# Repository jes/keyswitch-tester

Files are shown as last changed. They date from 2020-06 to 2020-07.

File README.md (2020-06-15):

# Automatic keyboard switch tester

This is the code and CAD for the automatic keyboard switch tester.

You can learn more in my blog post at https://incoherency.co.uk/blog/stories/keyswitch-tester.html

It is not spectacularly well designed, so if you want to make one you might instead consider designing an improved version.

You can [watch a video of it in action](https://www.youtube.com/watch?v=jl0PIKjTmjM).

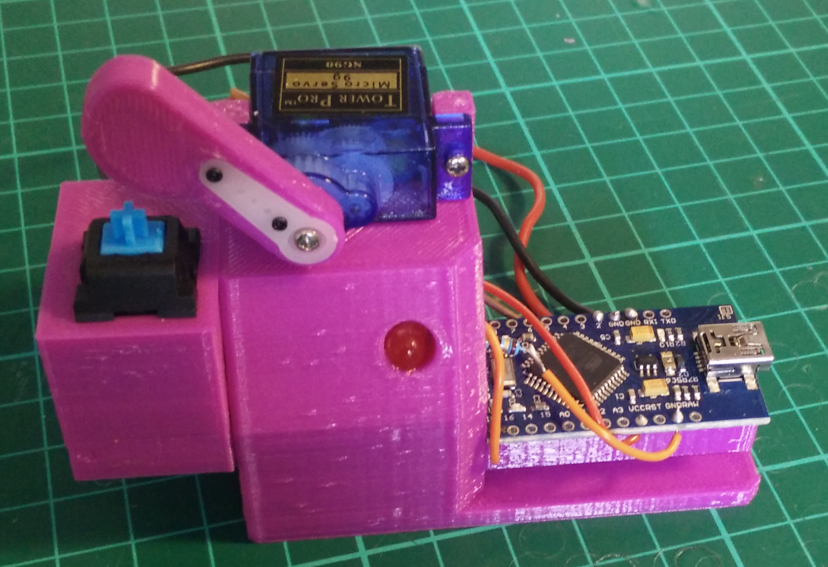
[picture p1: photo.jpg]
Photograph of device


## Assembly instructions

Print 1 each of servohorn.stl, keyswitch-tester.stl, and a holder for whatever type of switch you're using (e.g. cherry-holder.stl).

If you need to make a custom switch holder, you can either start from scratch, or start from BlankHolder in keyswitch-tester.FCStd, or
start from blank-holder.stl in other CAD software. Remember that in addition to holding the switch, you also need to be able to
route wires out.

You'll also need:

 - 1x micro servo (Tower Pro SG90 or compatible)
 - 1x Arduino (I suggest Nano, Pro Micro, or similar)
 - Some short lengths of wire

Optional:

 - 5x M3 threaded insert
 - 1x LED
 - 1x resistor for the LED (e.g. 470 Ohm)

Fit the threaded inserts to the main body by holding them with tweezers while pressing down gently with a hot soldering iron. If you don't
want to use threaded inserts you can just use slightly larger screws and thread directly into the plastic. The hole is about 4mm across.

Super-glue the Arduino to the lower deck, and the LED into the hole. Screw the servo to the mounts on the upper deck. Screw the servo
arm extension on to the servo horn, and fit it to the servo.

Solder the black/brown wire from the servo to one of the GND pins, the red wire to the VCC pin, and the yellow/orange wire
to pin 9.

Solder the resistor to the negative lead of the LED, and a wire from the resistor to another GND pin. Solder the positive lead
of the LED to pin 10. If you don't want to use an LED, the device will still work, you just won't get visual feedback of when
the switch has been pressed.

Solder a loose wire to another GND pin, and another loose wire to pin 2. Solder the other end of the loose wires to whatever
switch you're trying to test. Remain mindful of the fact that you need to be able to fit the switch in the holder, so do these
operations in a sensible order.

Fit your switch to your holder, and screw it to the end plate of the tester.

## Usage instructions

Plug in the Arduino and upload the code. If the servo is stalling, or is not moving through the correct range of motion, then you can
either remove and re-fit the servo arm at a different angle, or adjust the "servomin" and "servomax" parameters in the code.

Once it's clicking your switch properly (which you can verify by looking at the LED you fitted), then you can connect your logging
program to the USB serial port to collect data.

## Contributing

Please contribute any and all changes or fixes. If your contribution does not conveniently fit with the rest of the project, I'll stick
it in a `contrib/` directory so that other people can still get it.

I'm particularly interested in holders for different types of switch, and an improved design for the main body of the tester that meets either
or both of the following:

1. use less plastic (print faster)

2. allow the servo arm to reach its full range of motion instead of crashing into the deck

## Contact

You can email me at james@incoherency.co.uk, or read my blog at https://incoherency.co.uk/

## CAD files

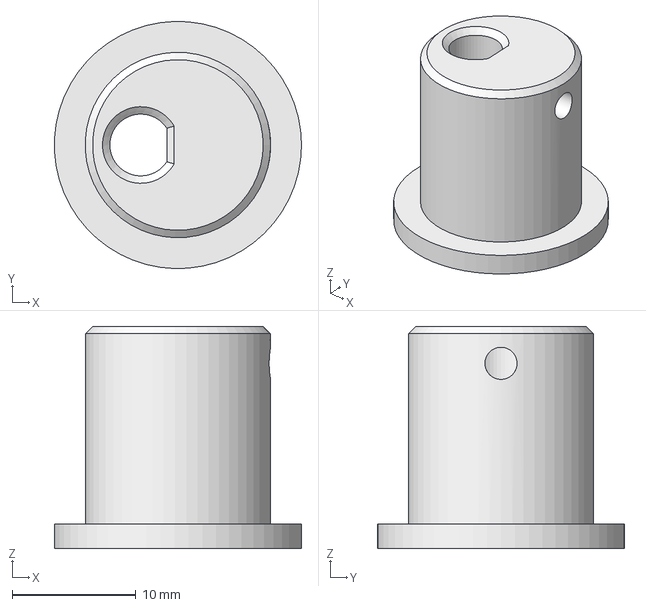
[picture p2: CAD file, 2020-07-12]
bigmachine/eccentricbush.FCStd
20.0 x 20.0 x 18.0 mm

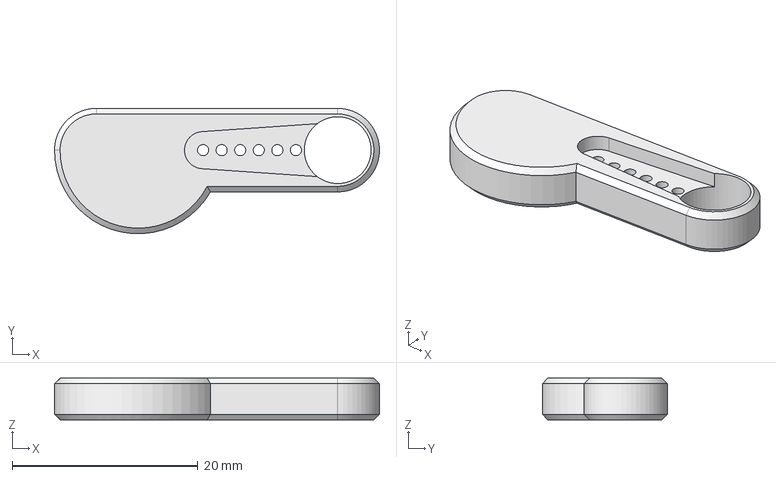
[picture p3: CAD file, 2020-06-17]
servohorn.FCStd
35.0 x 13.5 x 4.50 mm

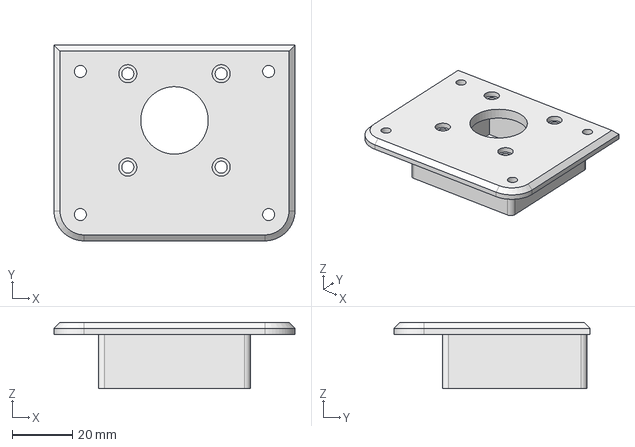
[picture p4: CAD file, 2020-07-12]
bigmachine/steppermount.FCStd
80.0 x 65.0 x 22.0 mm

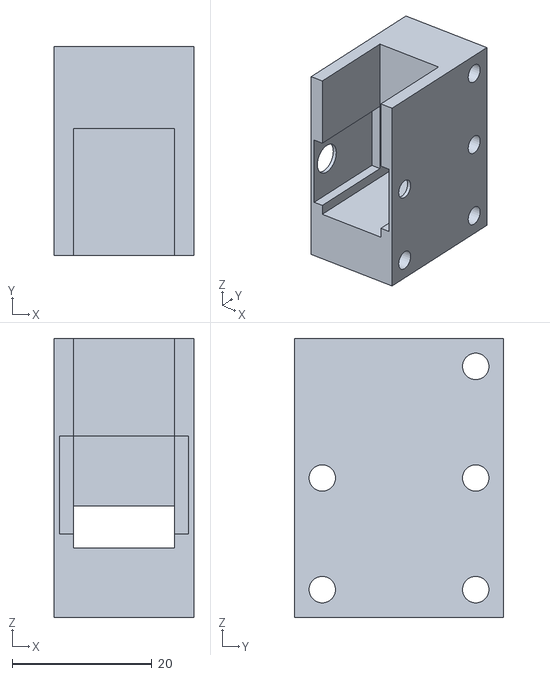
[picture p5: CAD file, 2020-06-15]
jes-holder.stl
20.0 x 30.0 x 40.0

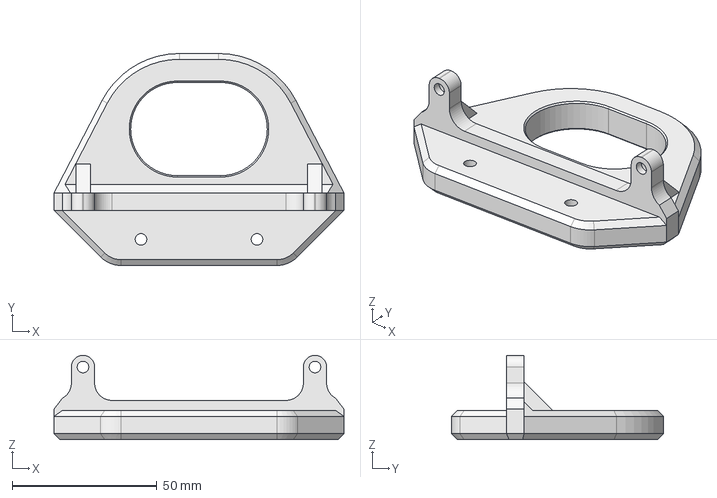
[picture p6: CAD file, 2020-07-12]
bigmachine/yoke.FCStd
100.0 x 73.1 x 29.0 mm

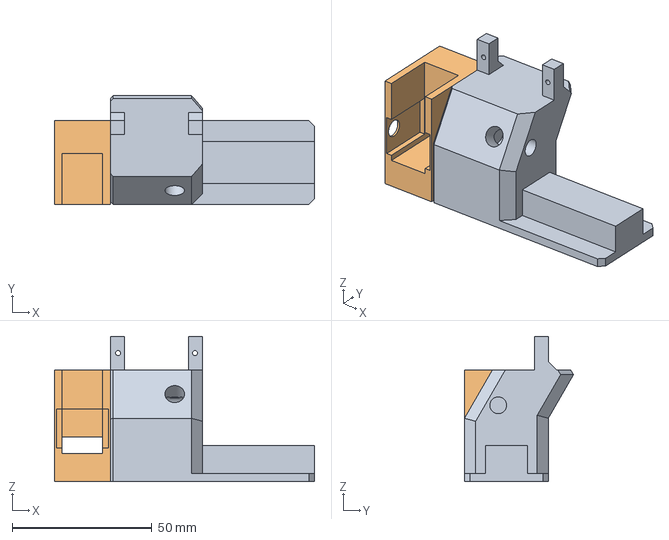
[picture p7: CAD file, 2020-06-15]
keyswitch-tester.FCStd
93.0 x 39.0 x 52.0 mm
JesHolder

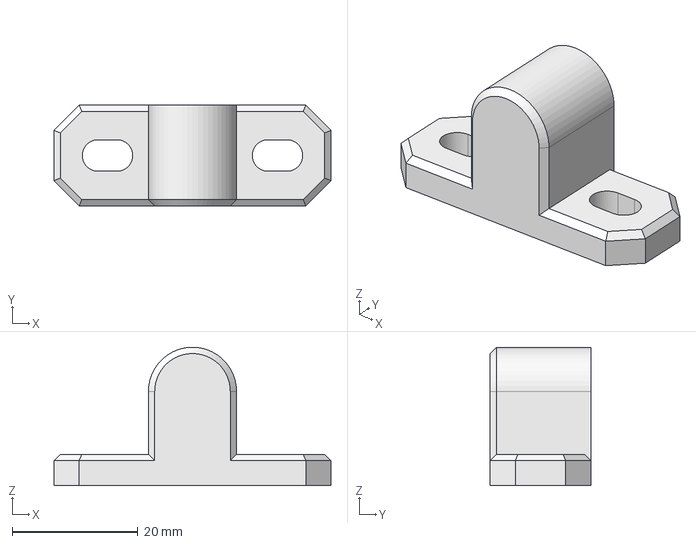
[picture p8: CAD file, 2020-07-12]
bigmachine/rodmount.FCStd
44.0 x 16.0 x 22.0 mm

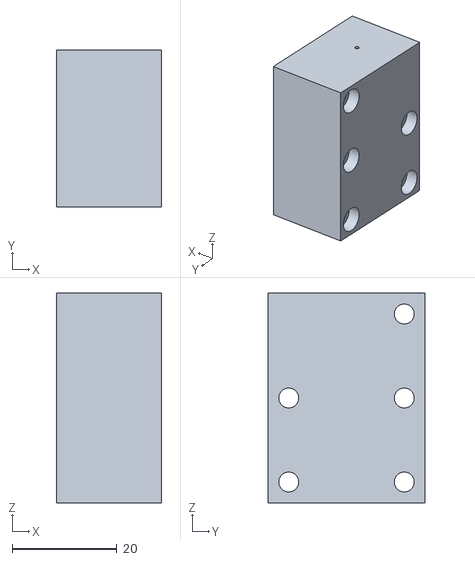
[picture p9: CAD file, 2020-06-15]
blank-holder.stl
20.0 x 30.0 x 40.0

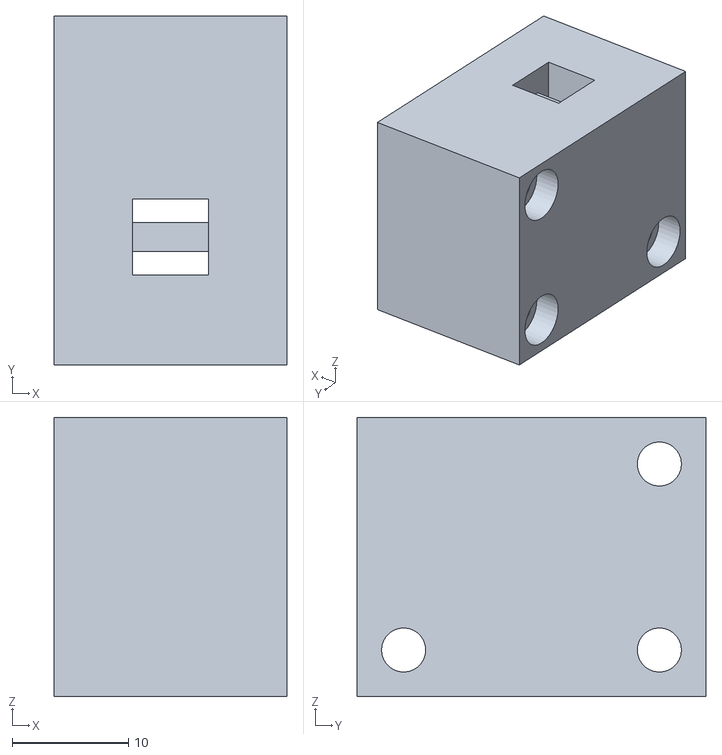
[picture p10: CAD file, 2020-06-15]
6mm-microswitch-holder.stl
20.0 x 30.0 x 24.0

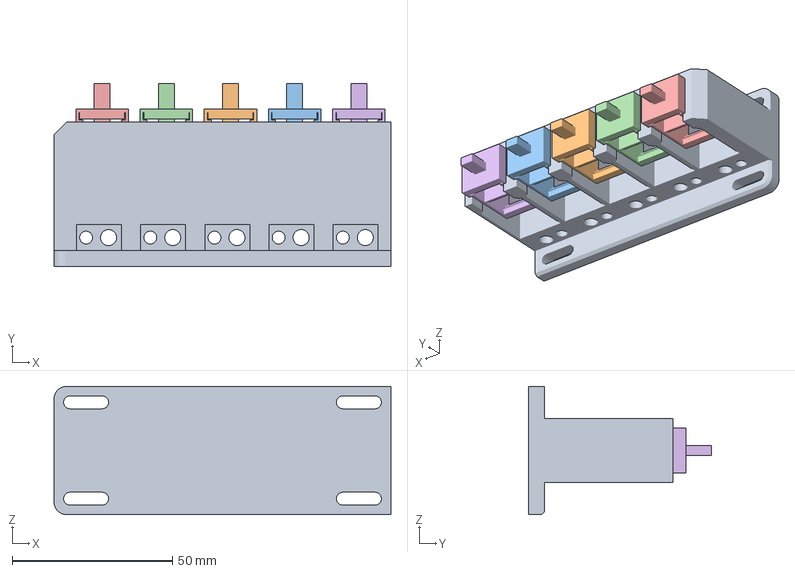
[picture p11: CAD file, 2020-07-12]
bigmachine/switchholder.FCStd
105.0 x 57.0 x 40.0 mm
v10
v011
v012
v013
v014

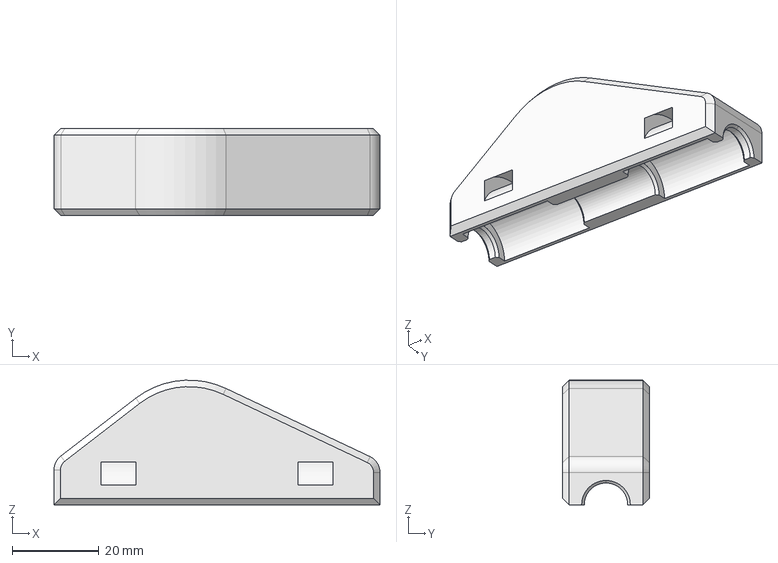
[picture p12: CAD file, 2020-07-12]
bigmachine/bearingmount.FCStd
75.0 x 20.0 x 28.7 mm

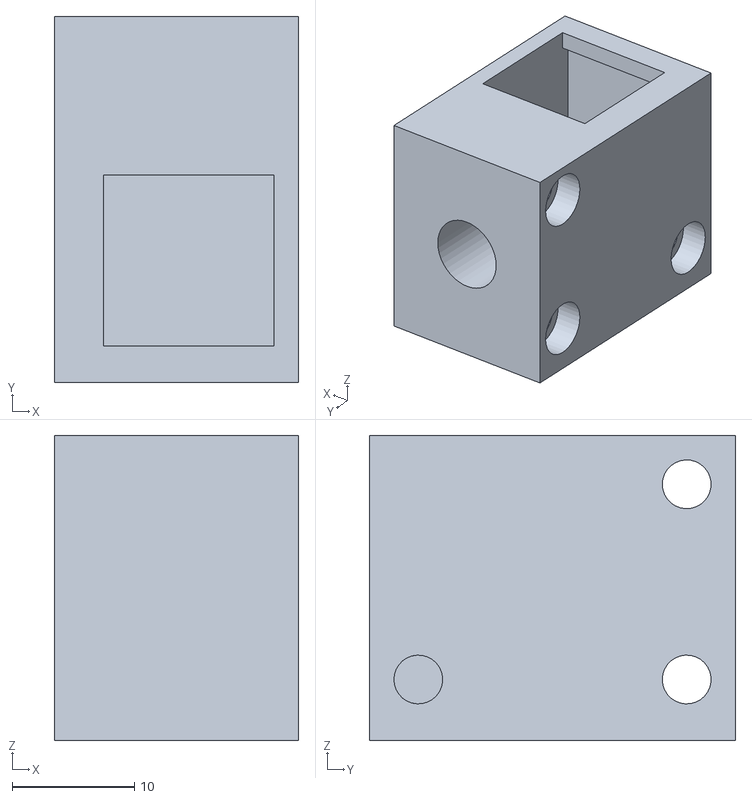
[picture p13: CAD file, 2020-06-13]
cherry-holder.stl
20.0 x 30.0 x 25.0

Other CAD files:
keyswitch-tester.stl
servohorn.stl

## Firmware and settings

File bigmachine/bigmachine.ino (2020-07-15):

#include <TimerOne.h>

#define BUFSZ 128
#define NSWITCHES 10

volatile unsigned long last_halfstep;
volatile int halfstepcount = 0;
volatile bool stepState;

int enablePin = 9;
int stepPin = 3;
bool enabled = false;

bool switchstate[NSWITCHES];
int switchpin[NSWITCHES];

int curspeed = 0; // steps/sec
int targetspeed = 2000; // steps/sec
int accel = 10; // steps/sec per millisecond
int steps_per_rev = 200;
int halfsteps_per_rev = steps_per_rev * 2;
unsigned long micros_per_halfstep;

void setup()
{  
  Serial.begin(115200);

  switchpin[0] = 4;
  switchpin[1] = 10;
  switchpin[2] = 15;
  switchpin[3] = A1;
  switchpin[4] = 5;
  switchpin[5] = 14;
  switchpin[6] = 16;
  switchpin[7] = A2;
  switchpin[8] = A3;
  switchpin[9] = A0;

  for (int i = 0; i < 10; i++) {
    pinMode(switchpin[i], INPUT_PULLUP);
  }

  pinMode(stepPin, OUTPUT);
  pinMode(enablePin, OUTPUT);

  curspeed = 0;
  disableStepper();

  Timer1.initialize(0);
  Timer1.stop();
  Timer1.attachInterrupt(timerIsr);
}

// called by timer every time we want to do half a step (i.e. toggle step pin)
void timerIsr() {
  last_halfstep = micros();
  stepState = !stepState;
  digitalWrite(stepPin, stepState);
  halfstepcount = (halfstepcount + 1) % halfsteps_per_rev;
}

void loop()
{  
   accelerate();
   communicate();
   scanSwitches();
}

void scanSwitches() {
  for (int i = 0; i < NSWITCHES; i++) {
    int state = !digitalRead(switchpin[i]);
    if (state != switchstate[i]) {
      switchstate[i] = state;
      unsigned long last = last_halfstep;
      int count = halfstepcount;
      double proportion = ((double)(micros() - last) / (double)micros_per_halfstep);

      // XXX: think this can be out of range due to race window between grabbing last_halfstep and halfstepcount?
      // if proportion > 1 then it means halfstepcount will already haev increased betwee grabbing last_halfstep and calculating
      // proportion, so we can set the proportion to 0 and assume we already have the updated halfstepcount.
      if (proportion > 1)
        proportion = 0;

      double halfsteps = count + proportion;
      Serial.print(halfsteps/2); Serial.print(state ? '+' : '-'); Serial.println(i);
    }
  }
}

void accelerate() {
   static unsigned long last_accel;

   if (!enabled)
     return;
   
   if (millis() > last_accel && curspeed != targetspeed) {
    last_accel = millis();
    if (targetspeed > curspeed+accel) {
      curspeed += accel;
    } else if (targetspeed < curspeed-accel) {
      curspeed -= accel;
    } else {
      curspeed = targetspeed;
    }
    micros_per_halfstep = 500000 / curspeed;
    Timer1.setPeriod(micros_per_halfstep);
   }
}

void enableStepper() {
  enabled = true;
  digitalWrite(enablePin, LOW);

  halfstepcount = 0;
  Timer1.start();
}

void disableStepper() {
  enabled = false;
  digitalWrite(enablePin, HIGH);
  
  Timer1.stop();

  stepState = false;
  digitalWrite(stepPin, stepState);
}

void communicate() {
  static char buf[BUFSZ];
  static int p;
  static bool seen_start;

  if (seen_start == false && halfstepcount == 0) {
    Serial.println(".");
    seen_start = true;
  }
  if (halfstepcount != 0)
    seen_start = false;
  
  while (Serial.available() > 0) {
    char c = Serial.read();
    if (c == '\r' || c== '\n' || p == BUFSZ-1) {
      buf[p++] = 0;
      serialCommand(buf);
      p = 0;
    } else {
      buf[p++] = c;
    }
  }
}

void serialCommand(char *buf) {
  char **params = split(buf);

  if (strcmp(params[0], "help") == 0) {
    Serial.print(
      "commands:\r\n"
      "   help           - show help\r\n"
      "   speed RPM      - set speed\r\n"
      "   start          - start motor\r\n"
      "   stop           - stop motor\r\n"
    );
      
  } else if (strcmp(params[0], "speed") == 0) {
    if (!params[1]) {
      Serial.println("error: usage: speed RPM");
      return;
    }
  
    unsigned long rpm = atoi(params[1]);
    if (rpm < 1 || rpm > 2000) {
      Serial.println("error: rpm must be between 1 and 2000");
      return;
    }

    targetspeed = rpm * steps_per_rev / 60;
    
  } else if (strcmp(params[0], "start") == 0) {
    enableStepper();
    
  } else if (strcmp(params[0], "stop") == 0) {
    curspeed = 0;
    disableStepper();

  }
}

// replace each space in buf with a \0, and return a (static!) nul-terminated array of pointers to the string parts
char **split(char *buf) {
  static char *parts[16];
  int n = 0;
  
  char *p = buf;
  while (*p && n < 15) {
    parts[n++] = p;
    while (*p && *p != ' ')
      p++;
    if (*p == ' ')
      *(p++) = 0;
  }
  parts[n++] = 0;
  
  return parts;
}

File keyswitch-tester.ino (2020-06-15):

/* Keyboard switch tester
 * 
 * James Stanley 2020
 * 
 * Pin assignments:
 *   9 - servo
 *   10 - status LED
 *   2 - switch (normally open, connect to ground to activate)
 * 
 * Output over serial at 9600 baud
 */

#include <Servo.h>

Servo servo;

int servopin = 9;
int ledpin = 10;
int switchpin = 2;

int servomin = 1500;
int servomax = 2000;
float servospeed = 0.2; // servo usecs per ms
float servomaxspeed = 4; // speed to reset

float servopos;

void setup() {
  servo.attach(servopin);
  pinMode(ledpin, OUTPUT);
  pinMode(switchpin, INPUT_PULLUP);
  writeServo(servomin);
  Serial.begin(9600);
  delay(1000); // wait for serial port to work?
  Serial.print("keyswitch-tester begins\n");
}

void loop() {
  if (!pressed()) {
    cycle();
  } else {
    busy_delay(1000);
  }
}

void busy_delay(unsigned long ms) {
  unsigned long startms = millis();
  unsigned long endms = startms + ms;

  // check that "start <= millis()" so that we don't wait forever when millis() overflows
  while (millis() < endms && startms <= millis()) {
     pressed(); // just keep the led status up to date
  }
}

bool pressed() {
  int state = !digitalRead(switchpin);
  digitalWrite(ledpin, state);
  return state;
}

void writeServo(float val) {
  servopos = val;
  servo.writeMicroseconds(val);
}

void resetServo() {
  float oldpos = servopos;
  writeServo(servomin);
  busy_delay((oldpos - servomin) / servomaxspeed); // give the servo time to get back
}

void cycle() {
  unsigned long lastms = millis();
  float pos = servopos;
  
  while (!pressed() && pos < servomax) {
    unsigned long now = millis();
    if (now < lastms) { // time overflow: bail out and start again
      resetServo();
      return;
    }
    pos = pos + (now - lastms) * servospeed;
    lastms = millis();
    
    if (pos > servomax)
      pos = servomax;
    writeServo(pos);
  }

  if (pos < servomax) {
    Serial.print("OK "); Serial.print((int)pos); Serial.print(" ");
    back_cycle();
  } else {
    Serial.print("FAIL "); Serial.print((int)pos); Serial.print("\n");
    resetServo();
  }
}

void back_cycle() {
  unsigned long lastms = millis();
  float pos = servopos;

  busy_delay(100);
  
  while (pressed() && pos > servomin) {
    unsigned long now = millis();
    if (now < lastms) { // time overflow: bail out and start again
      Serial.println("OK (timewrap)\n");
      resetServo();
      return;
    }
    pos = pos - (now - lastms) * servospeed;
    lastms = millis();
    
    if (pos < servomin)
      pos = servomin;
    writeServo(pos);
  }

  if (pos > servomin) {
    Serial.print("OK "); Serial.print((int)pos); Serial.print("\n");
    resetServo();
  } else {
    Serial.print("FAIL "); Serial.print((int)pos); Serial.print("\n");
    resetServo();
  }
}

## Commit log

2020-06-13 Add CAD files
    [cherry-holder.stl, keyswitch-tester.FCStd, keyswitch-tester.stl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]
2020-06-14 Reset switch faster, various other fixes
    [keyswitch-tester.FCStd, servohorn.FCStd]
2020-06-14 Add servohorn STL
    [servohorn.FCStd, servohorn.stl]
2020-06-15 More switch holders
    [6mm-microswitch-holder.stl, blank-holder.stl, keyswitch-tester.FCStd]
2020-06-15 Note on wires
2020-06-15 Fix centre point on blank holder
    [6mm-microswitch-holder.stl, blank-holder.stl, keyswitch-tester.FCStd]
2020-06-15 Add jes-holder, increase motion range
    [jes-holder.stl, keyswitch-tester.FCStd]
2020-06-17 Make servohorn thinner as it is rubbing on servo
    [servohorn.FCStd, servohorn.stl]
2020-07-12 Add CAD files for new machine
    [bearingmount.FCStd, eccentricbush.FCStd, rodmount.FCStd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]
2020-07-13 Fix pin assignments
